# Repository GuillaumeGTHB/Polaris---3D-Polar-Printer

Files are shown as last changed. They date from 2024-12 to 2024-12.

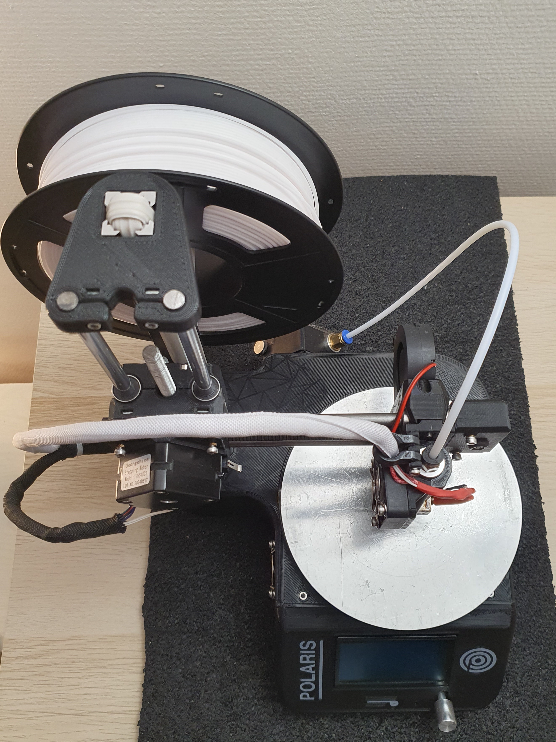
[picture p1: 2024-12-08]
Pictures/20241208_211539.jpg

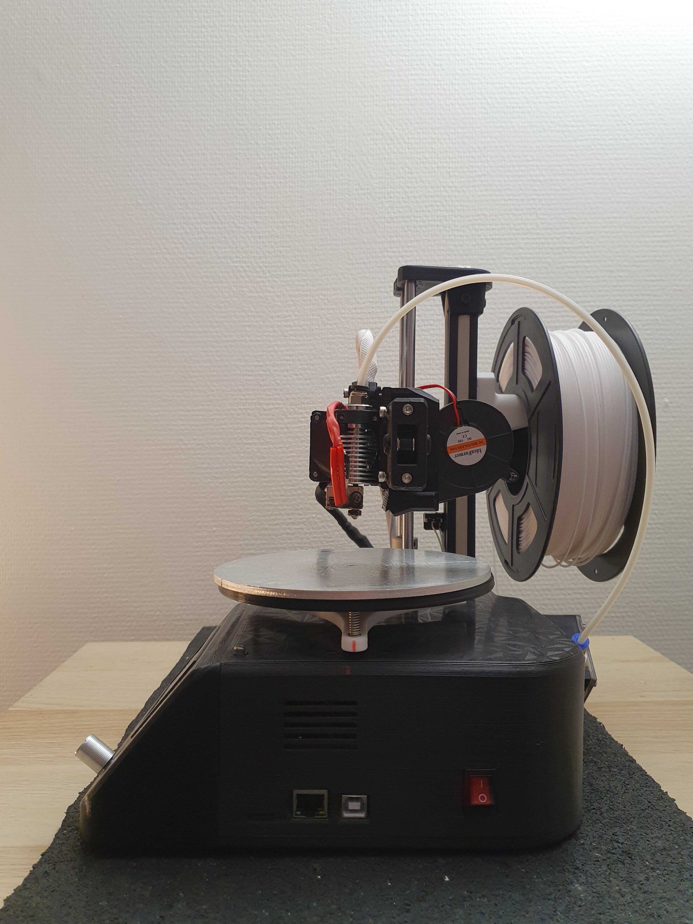
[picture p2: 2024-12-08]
Pictures/20241208_211434.jpg

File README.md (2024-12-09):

# Polaris - 3D Polar Printer !
**A video showing the assembly of the printer is available here:**
+ **https://www.youtube.com/watch?v=0U_K4j7AWgo**<br />

**Videos of normal & vase mode here:**
+ **https://www.youtube.com/shorts/QpnZfWZlSms**<br />
+ **https://www.youtube.com/shorts/CVd2ITZNg2Q**<br />

**Print bed size needed: 210x240mm**

<p align="center">



</p>

If you like my work, you can help me by buying me a coffee, thank you! <br />
*https://buymeacoffee.com/guillaumehy or [paypal.me/guillaumehaouy](https://www.paypal.com/paypalme/guillaumehaouy)* <br />
*I should point out that I am a 20 year old student, it takes me a huge amount of time so don't be too harsh and impatient with me !* <br />

**Step files are include !**
<p align="center">



</p>

## 1. Introduction
*Ever since I discovered polar printers, they have always intrigued me. I had a lot of trouble understanding how movement was done in a polar environment, so I decided to make one! I based my design on the use of old 3D printing parts, in order to obtain an inexpensive machine. The other constraint was being able to print everything on my 210x240mm plate, which wasn't very easy, especially for the chassis... Anyway, it was supposed to be a small personal project but when I presented it on Reddit, so many people were interested that here are all of my files! <br />
Enjoy ;)*

## 2. Bill of Materials (BOM):
**<ins>BOM:</ins>**
<p align="center">

</p>

## 3. Technical details of the Polaris 3D Polar Printer :
+ Print area: 150x150x105mm <br />
+ Motherboard: MKS Sbase v1.3 or SKR E3 v3.0 <br />
+ Screen: LCD12864 or TFT35 <br />
+ Speeds: around 40mm/s, not tested above <br />
+ Price: around 100$, much less if you already have equipment <br />
+ No heatbed ! <br />

## 4. Marlin logos
<p align="center">



</p>

## 5. Pictures of Normal & Vase mode (print in center is available, but no pictures yet)
<p align="center">



 

</p>

## 6. Schematic
<p align="center">

</p>

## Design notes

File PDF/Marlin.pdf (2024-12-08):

## Marlin

Here is the polar code section in “configuration.h” of Marlin bugfix 2.1.x. You can find all my modifications made (configuration.h and configuration_adv.h) by pressing “ctrl F” then “Polaris”:

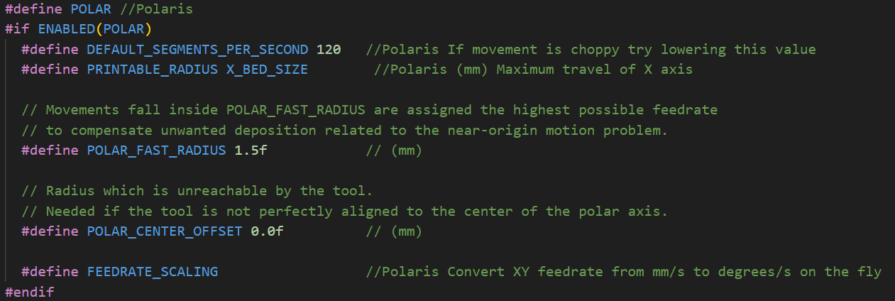
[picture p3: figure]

WARNING !!!
The firmware for the TFT35 screen and the SKR E3 v3.0 motherboard is not provided because not having this hardware, I was not able to test it ! My version of the firmware is made for an LCD12864 screen and an Sbase v1.3 motherboard, so you will have to make modifications if you don’t want use an Sbase/LCD12864

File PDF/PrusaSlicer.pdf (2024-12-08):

## PrusaSlicer

Open PrusaSlicer and : → Menu → Files → Import → Import the configuration “PLA_Polaris.ini & PLA_Vase_mode_Polaris.ini”
You should have this :

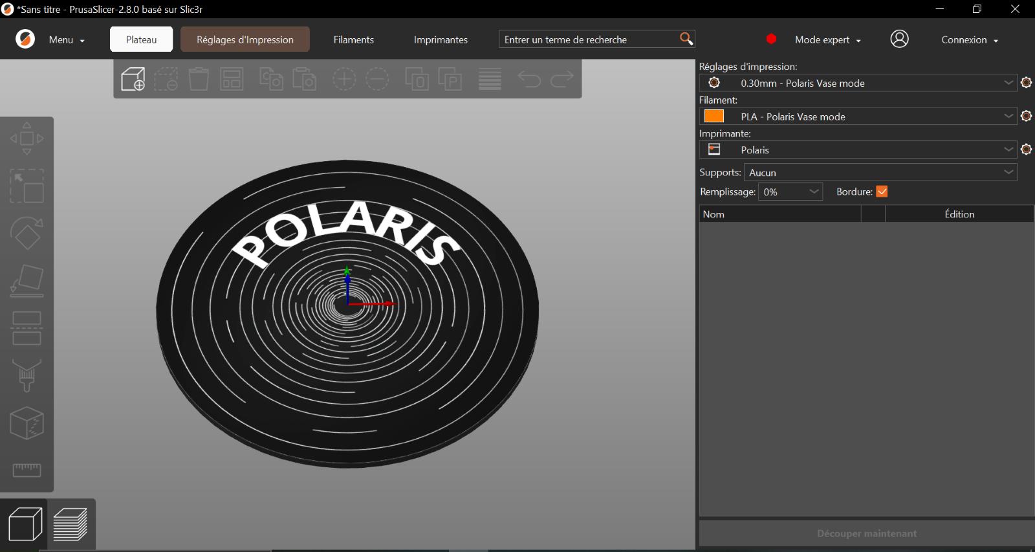
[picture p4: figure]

It has two types of settings, one for prints at the center-radius of the platen, the other for vase mode.

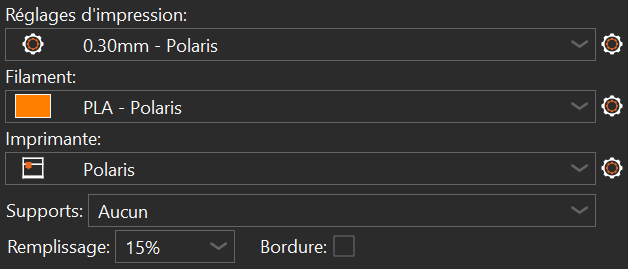
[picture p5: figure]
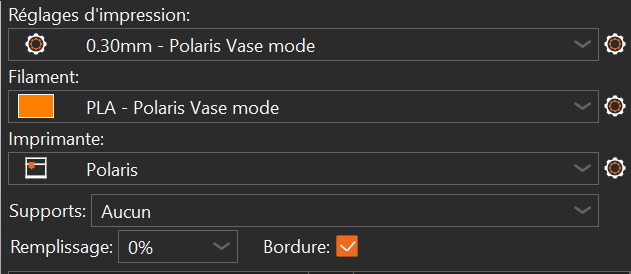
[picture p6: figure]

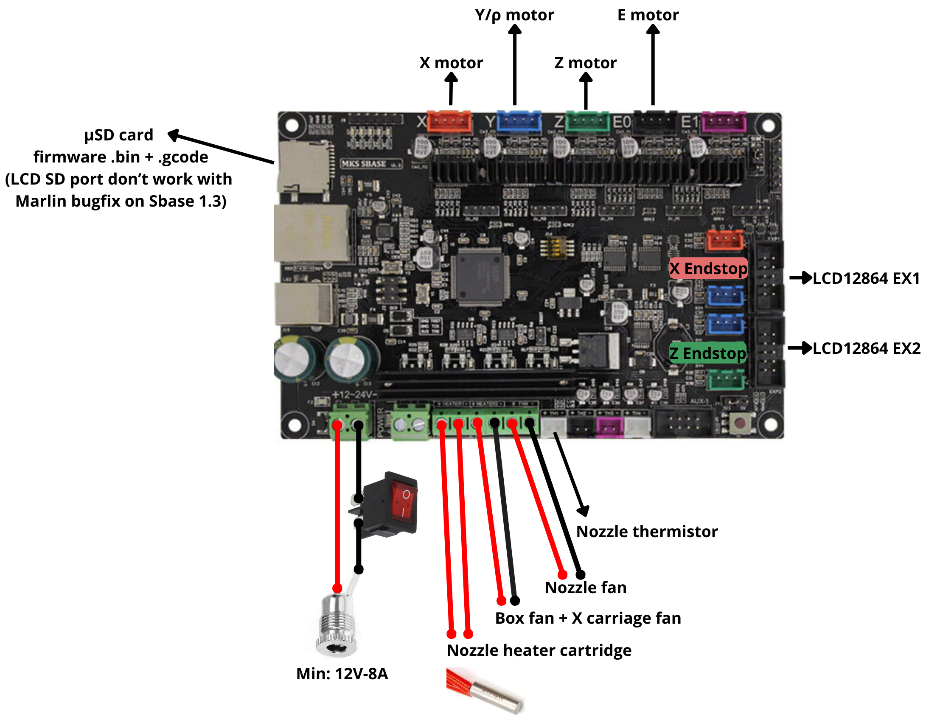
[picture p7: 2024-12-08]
Schema.png

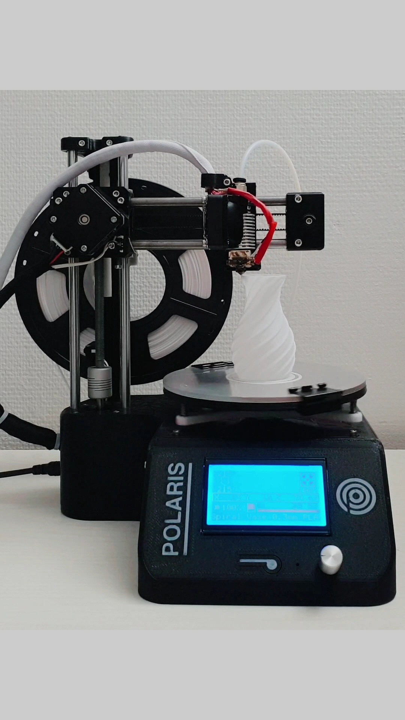
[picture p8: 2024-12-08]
Pictures/VideoCapture_20241208-214109.jpg

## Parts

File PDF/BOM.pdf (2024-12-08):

Name | Quantity | Links (unaffiliated) | Total price (approximately)
Fan 40x10mm 12v | 2 | / | $ 2,00
Radial fan 50x15mm 12v | 1 | / | $ 1,50
E3Dv6 bowden 12v | 1 | / | $ 7,50
MKS Sbase v1.3 | 1 | (no longer produced, need to modify box .step files to use another) | /
Fan guard (optional) | 2 | / | $ 1,50
5 to 8mm coupler | 1 | / | $ 1,50
Nema 17 (normal or pancake) | 3 | / | $ 22,00
Nema 17 Pancake | 1 | / | $ 7,00
Mini endstop | 2 | https://fr.aliexpress.com/item/32811306212.html | $ 2,00
150mm aluminium plate | 1 | https://fr.aliexpress.com/item/1005006307340025.html | $ 10,00
LM8UU | 6 | / | $ 5,00
GT2 belt 40cm | 1 | / | $ 3,00
608 bearing | 4 | / | $ 4,00
2020 profile 300mm | 1 | https://fr.aliexpress.com/item/1005006975134393.html | $ 6,00
Bowden extruder | 1 | / | $ 5,00
PTFE Bowden 40cm 4-2mm | 1 | / | $ 1,50
8x240mm smooth rod | 2 | / | $ 7,50
8x200mm smooth rod | 2 | / | $ 6,00
GT2 80T Pulley 8mm bore | 1 | https://fr.aliexpress.com/item/1005007541344843.html | $ 5,00
GT2 Loop belt 234mm | 1 | https://fr.aliexpress.com/item/1005005787282420.html | $ 3,00
Cable sheath 8mm | 1 | https://fr.aliexpress.com/item/1005006912674049.html | $ 1,50
GT2 16T 3mm bore pulley | 1 | / | $ 1,50
GT2 16T 5mm bore motor pulley | 1 | / | $ 1,50
KCD1 250V 10A Switch | 1 | https://fr.aliexpress.com/item/1005007077852530.html | $ 2,50
DC-099 10A power socket | 1 | https://fr.aliexpress.com/item/1005001368469076.html | $ 2,00
$ | 110,00
Difficult to be accurate on the number, I
suggest you buy a kit for M3 screws !
M8 nut | 1
M4 T-nut | 7
M3 square nut | 6
M3 nut | 12
Insert M2 | 2
Insert M3x4.2mm | 26
M2x12mm | 3
M3x6mm | 7
M3x8mm | 12
M3x10mm | 19
M3x12mm | 4
M3x16mm | 5
M3x18mm | 4
M3x20mm | 8
M3x25mm | 4
M3x30mm | 5
M4x8mm | 3
M4x12mm | 4
$~15

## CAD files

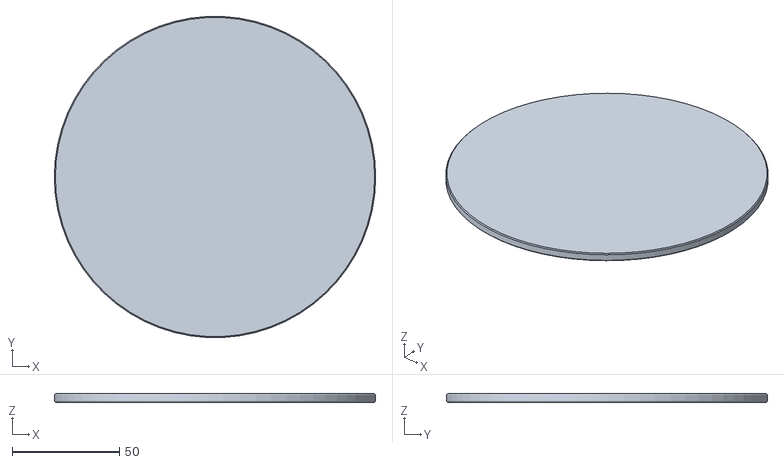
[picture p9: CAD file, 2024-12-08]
Prusa Slicer/Polaris_bed.STL
150.0 x 149.8 x 4.00

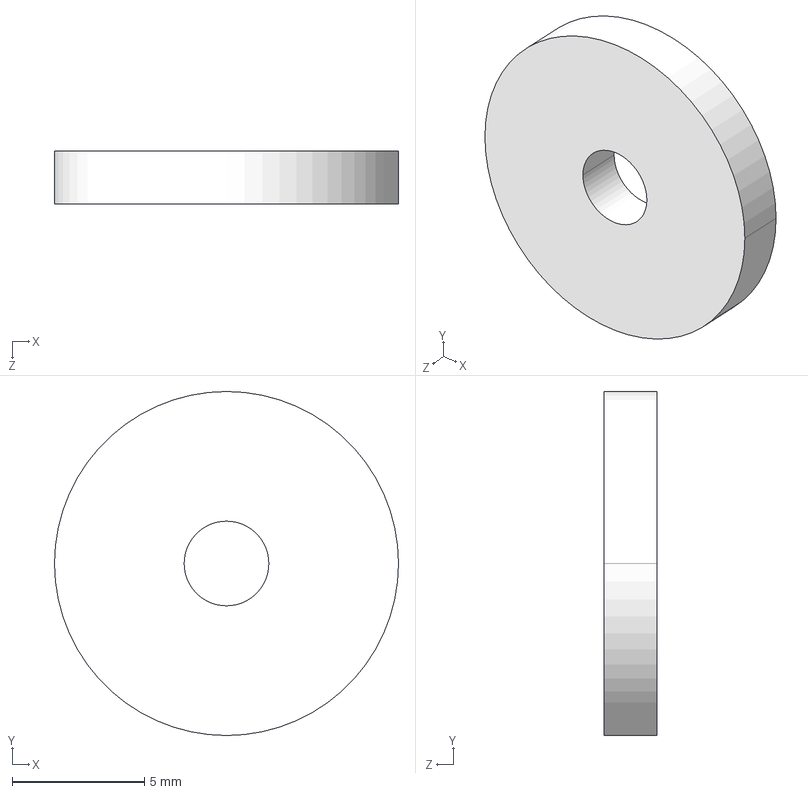
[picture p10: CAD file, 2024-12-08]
STEP/Common - Other parts/Bed_holder.STEP
13.0 x 13.0 x 2.00 mm

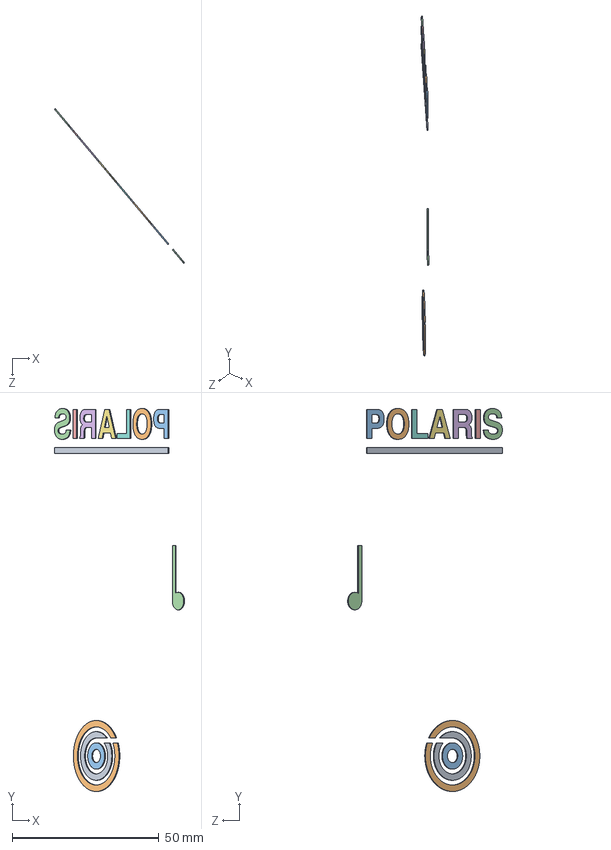
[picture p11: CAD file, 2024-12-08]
STEP/LCD12864/LCD_Box_Letters_LCD12864.STEP
44.3 x 130.4 x 52.7 mm

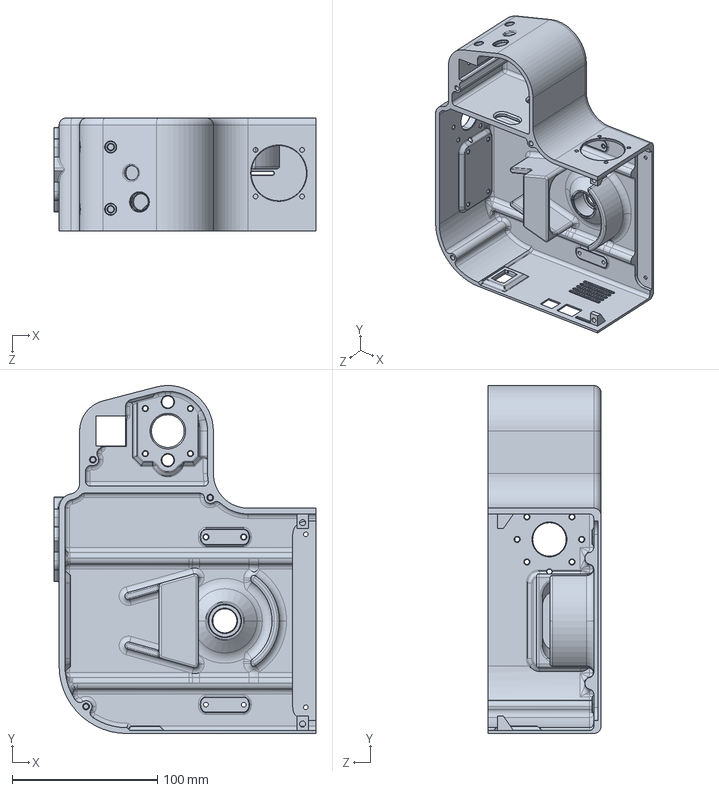
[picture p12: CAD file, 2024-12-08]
STEP/MKS SBASE v1.3/Box_MKS_SBASE.STEP
180.2 x 239.4 x 77.8 mm

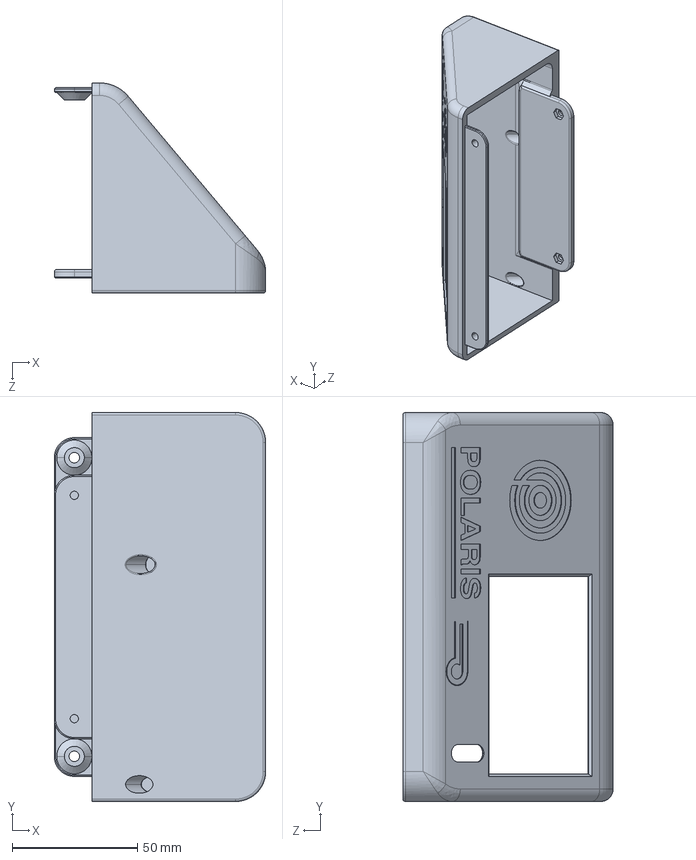
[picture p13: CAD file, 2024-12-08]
STEP/TFT35/LCD_Box_TFT35.STEP
84.3 x 155.0 x 83.8 mm

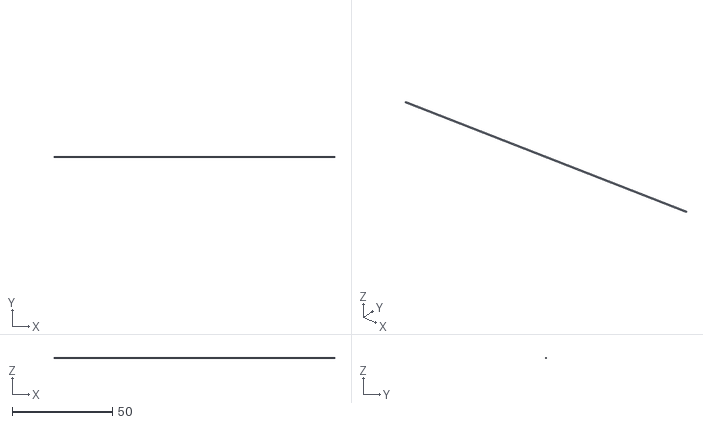
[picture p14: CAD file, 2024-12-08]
Y_calibration.stl
140.0 x 0.4 x 0.3

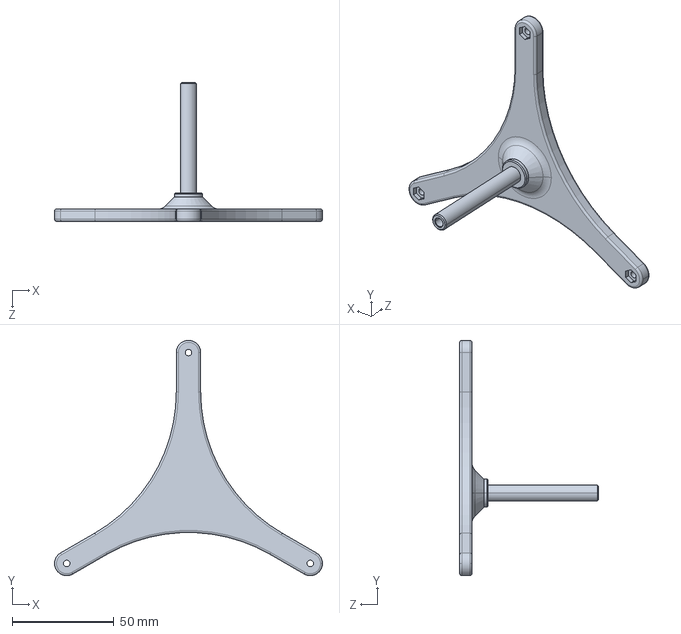
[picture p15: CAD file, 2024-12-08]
STEP/Common - Other parts/Bed_support.STEP
131.5 x 115.5 x 68.0 mm

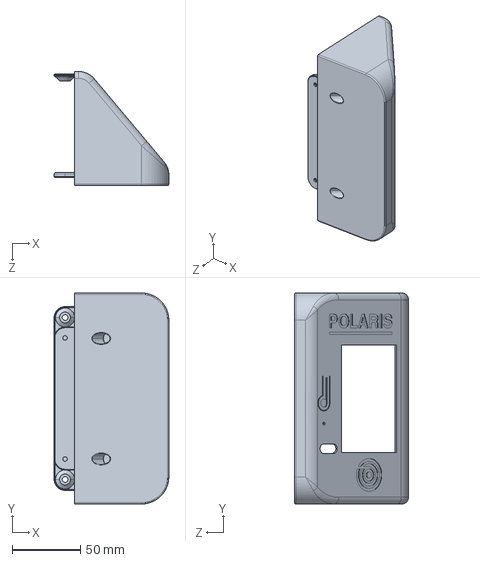
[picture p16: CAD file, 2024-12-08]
STEP/LCD12864/LCD_Box_LCD12864.STEP
84.3 x 155.0 x 83.8 mm

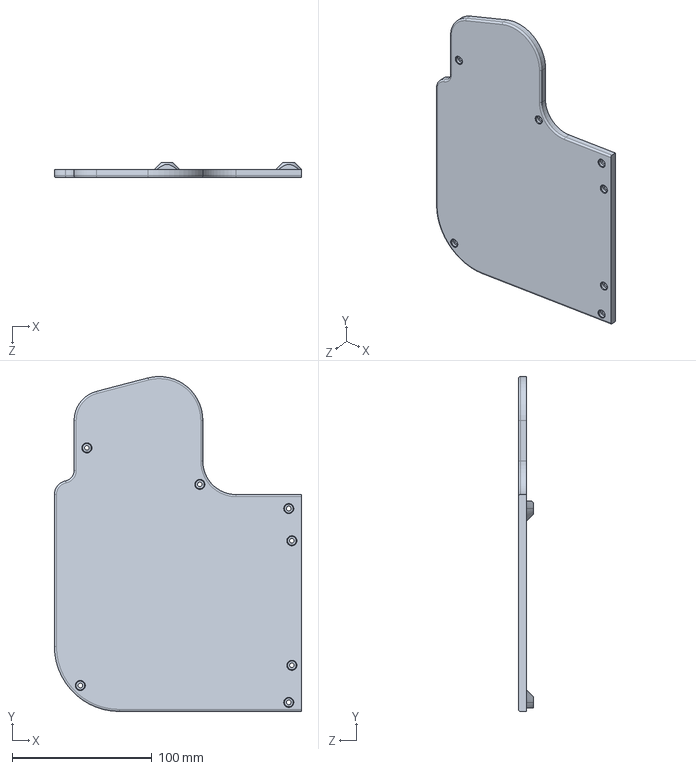
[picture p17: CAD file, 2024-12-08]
STEP/MKS SBASE v1.3/Base_MKS_SBASE.STEP
176.7 x 239.4 x 11.0 mm

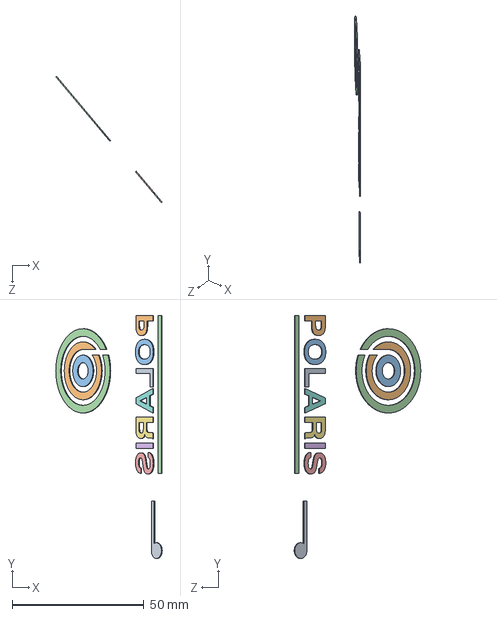
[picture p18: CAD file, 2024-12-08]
STEP/TFT35/LCD_Box_Letters_TFT35.STEP
40.4 x 92.2 x 48.1 mm

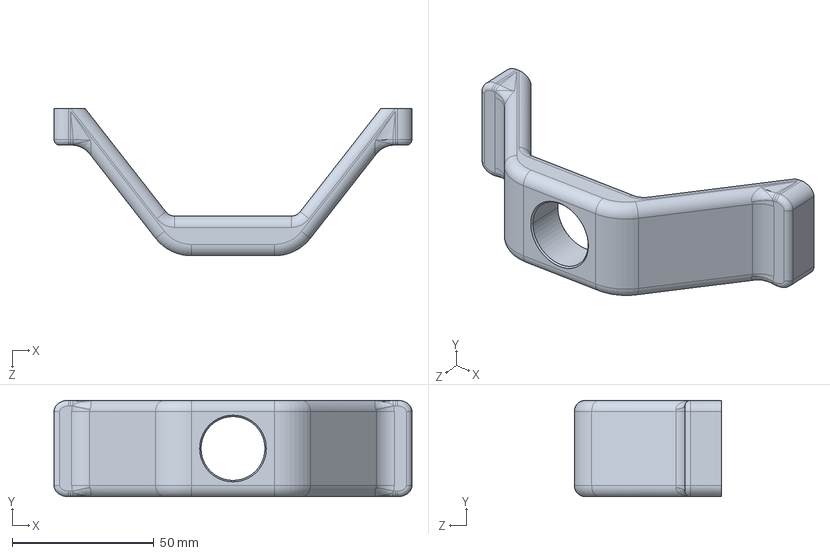
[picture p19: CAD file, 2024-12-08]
STEP/Common - Other parts/Bearing_clamp.STEP
126.3 x 34.0 x 52.0 mm

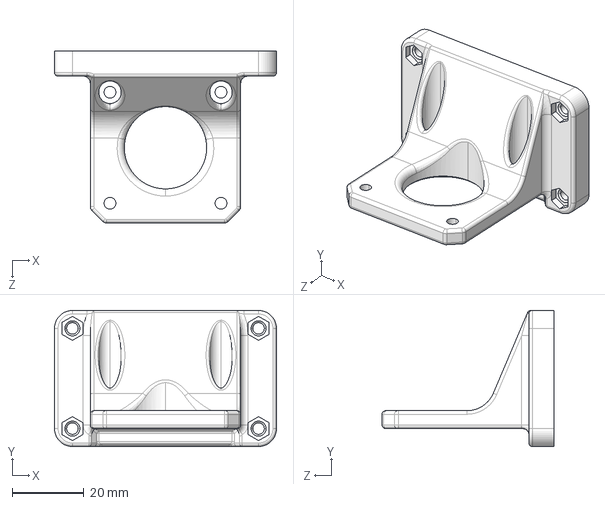
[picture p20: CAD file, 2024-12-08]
STEP/Common - Other parts/Motor_holder.STEP
62.0 x 38.0 x 48.0 mm

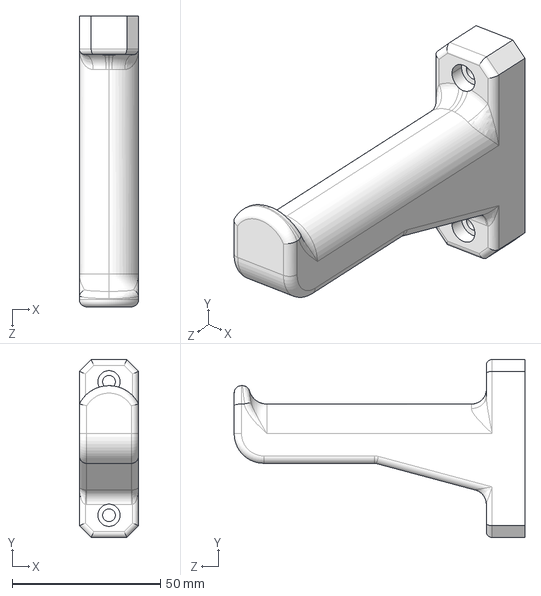
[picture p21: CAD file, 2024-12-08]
STEP/Common - Other parts/Spool_holder.STEP
20.0 x 60.0 x 98.0 mm

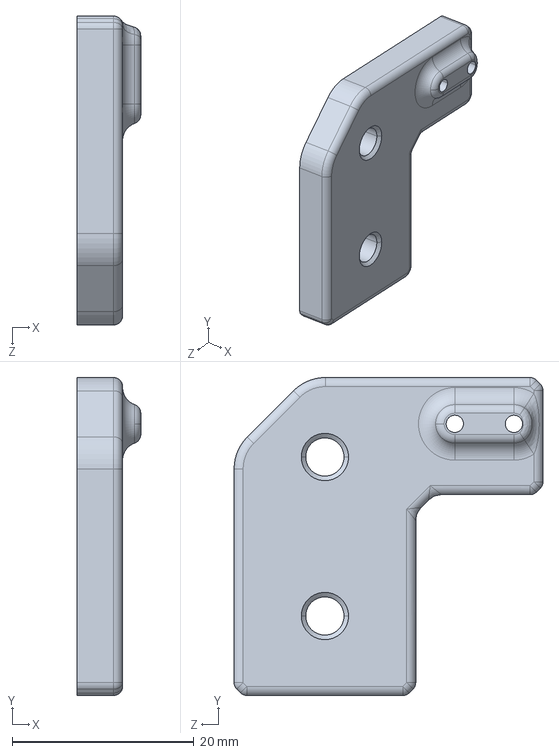
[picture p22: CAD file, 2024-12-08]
STEP/Common - Other parts/Z_endstop.STEP
7.00 x 35.0 x 34.0 mm

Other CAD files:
STEP/SKR E3 v3.0/Box_SKR_E3.STEP
STEP/SKR E3 v3.0/Base_SKR_E3.STEP
STEP/Common - Other parts/X_ending.STEP
STEP/Common - Other parts/X_cable.STEP
STEP/Common - Other parts/608zz_spacer.STEP
STEP/Common - Other parts/Bed.STEP
STEP/Common - Other parts/E3Dv6_carriage.STEP
STEP/Common - Other parts/E3Dv6_clamp.STEP
STEP/Common - Other parts/Mini_x_carriage.STEP
STEP/Common - Other parts/Motor_clamp.STEP
STEP/Common - Other parts/X_motor_holder_adjustable.STEP
STEP/Common - Other parts/Z_Endstop_axis.STEP
STEP/Common - Other parts/Z_top.STEP
STL/Common - Other parts/608zz_spacer.stl
STL/Common - Other parts/Bearing_clamp.stl
STL/Common - Other parts/Bed.stl
STL/Common - Other parts/Bed_holder.stl
STL/Common - Other parts/Bed_support.stl
STL/Common - Other parts/E3Dv6_carriage.stl
STL/Common - Other parts/E3Dv6_clamp.stl
STL/Common - Other parts/Mini_x_carriage.stl
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

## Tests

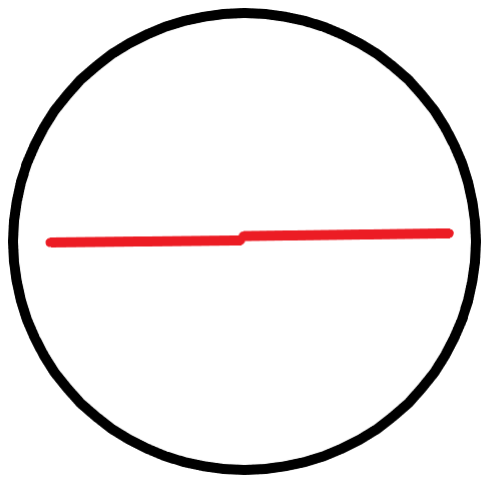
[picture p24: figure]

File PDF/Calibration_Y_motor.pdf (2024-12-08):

## Calibration of Y motor steps/°

For the rotary axis, it is not steps/mm but steps/°, which complicates things a little for calibration. Here's a technique I created but I don't know if it's the best...

The idea is therefore to print a continuous line crossing the diameter of the plate (the .stl file is “Y_calibration”, measuring 140*0.4*.4mm).

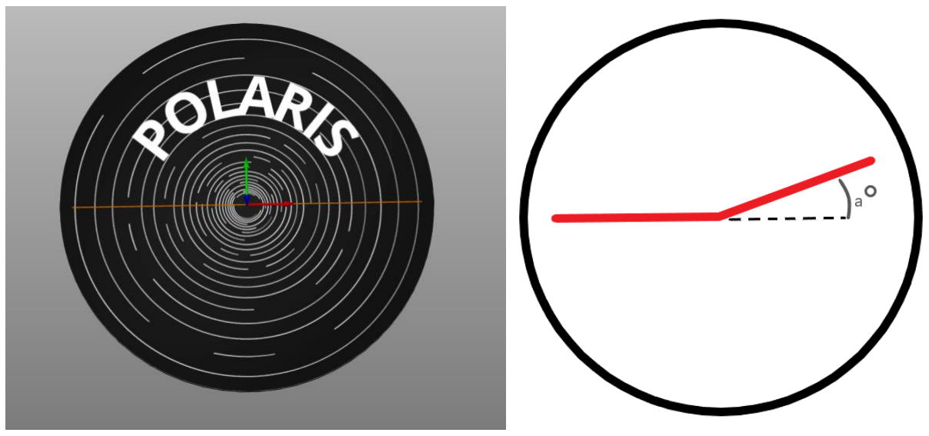
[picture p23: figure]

You will probably get something like this, because the motor will probably have turned too much, or not enough to complete a full 180° rotation. You will therefore measure the angle “α”.

- If it has turned too much, do this calculation :

steps⋅180
a+180
- If it hasn't turned enough, do this calculation : steps⋅180
a−180
If you then get something like below, your nozzle is not aligned with the center of the platen. This is a mechanical adjustment to be made from the support screws of the X axis rods.
